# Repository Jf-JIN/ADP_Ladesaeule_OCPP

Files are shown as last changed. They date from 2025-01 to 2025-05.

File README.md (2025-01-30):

# ADP_Ladesaeule_OCPP

###### Aufgabeliste

谷歌表格: https://docs.google.com/spreadsheets/d/17lJi9eMh2AS8moNZEip401Un4izFQ7JtTx4U8HynT7c/edit?usp=sharing

###### Liste der zu bestellenden Komponenten

谷歌表格：https://excel.cloud.microsoft/open/onedrive/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

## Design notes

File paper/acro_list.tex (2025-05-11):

\begin{acronym}[MPC] % Give the longest label here so that the list is nicely aligned
%\acro{}{}  %sort alphabaticly
\acro{CS}{Charging Station}
\acro{CSMS}{Charging Station Management System}
\acro{CP}{Charging Pilot}
\acro{PP}{Proximity pilot}
\acro{EV}{Electric Vehicle}
\acro{GUI}{Graphical User Interfaces}
\acro{OCPP}{Open Charge Point Protocol}
\acro{V2G}{Vehicle-to-Grid}
\acro{TX}{Transmission}
\acro{RX}{Receiver}
\end{acronym}

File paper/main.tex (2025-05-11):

\documentclass[
	english,
	ruledheaders=section,%Ebene bis zu der die Überschriften mit Linien abgetrennt werden, vgl. DEMO-TUDaPub
	class=report,% Basisdokumentenklasse. Wählt die Korrespondierende KOMA-Script Klasse
	thesis={type=Report},% Dokumententyp Thesis, für Dissertationen siehe die Demo-Datei DEMO-TUDaPhd
	accentcolor=9c,% Auswahl der Akzentfarbe
	custommargins=true,% Ränder werden mithilfe von typearea automatisch berechnet
	marginpar=false,% Kopfzeile und Fußzeile erstrecken sich nicht über die Randnotizspalte
	%BCOR=5mm,%Bindekorrektur, falls notwendig
	parskip=half-,%Absatzkennzeichnung durch Abstand vgl. KOMA-Script
	fontsize=11pt,%Basisschriftgröße laut Corporate Design ist mit 9pt häufig zu klein
	logofile={img/tuda_logo.pdf}, %Falls die Logo Dateien nicht vorliegen
]{tudapub}

% Der folgende Block ist nur bei pdfTeX auf Versionen vor April 2018 notwendig
\usepackage{iftex}
\ifPDFTeX
	\usepackage[utf8]{inputenc}%kompatibilität mit TeX Versionen vor April 2018
\fi

%%%%%%%%%%%%%%%%%%%
%Sprachanpassung & Verbesserte Trennregeln
%%%%%%%%%%%%%%%%%%%
\usepackage[ngerman, main=english]{babel}
% \usepackage[english, main=ngerman]{babel}
% % 中文支持
% \usepackage{fontspec}
% \usepackage{xeCJK}  % LuaLaTeX 也适用

% % 设置中文字体
% \setCJKmainfont{Noto Serif CJK SC}  % 适用于简体中文
% \setCJKsansfont{Noto Sans CJK SC}   % 无衬线字体
% \setCJKmonofont{Noto Sans Mono CJK SC} % 等宽字体

% \usepackage[autostyle]{csquotes}% Anführungszeichen vereinfacht

% Falls mit pdflatex kompiliert wird, wird microtype automatisch geladen, in diesem Fall muss diese Zeile entfernt werden, und falls weiter Optionen hinzugefügt werden sollen, muss dies über
% \PassOptionsToPackage{Optionen}{microtype}
% vor \documentclass hinzugefügt werden.
\usepackage{microtype}
\usepackage{subcaption}
%%%%%%%%%%%%%%%%%%%
%Literaturverzeichnis
%%%%%%%%%%%%%%%%%%%
\usepackage{biblatex}   % Literaturverzeichnis
\bibliography{bibliography}
\usepackage{breakurl}
\usepackage{xurl} 

%%%%%%%%%%%%%%%%%%%
%Paketvorschläge Tabellen
%%%%%%%%%%%%%%%%%%%
%\usepackage{array}     % Basispaket für Tabellenkonfiguration, wird von den folgenden automatisch geladen
\usepackage{tabularx}   % Tabellen, die sich automatisch der Breite anpassen
%\usepackage{longtable} % Mehrseitige Tabellen
%\usepackage{xltabular} % Mehrseitige Tabellen mit anpassbarer Breite
\usepackage{booktabs}   % Verbesserte Möglichkeiten für Tabellenlayout über horizontale Linien
\usepackage{graphicx}
\usepackage{pdfpages}
\usepackage{enumitem}
\usepackage{xcolor}

\usepackage{float} 
\usepackage[acronym]{glossaries}
\usepackage{caption}
\captionsetup{justification=centering}
% acronyms
\usepackage{acronym}

%其他引用库
\usepackage{hyperref}
\usepackage{url}

%%%%%%%%%%%%%%%%%%%
%Paketvorschläge Mathematik
%%%%%%%%%%%%%%%%%%%
%\usepackage{mathtools} % erweiterte Fassung von amsmath
%\usepackage{amssymb}   % erweiterter Zeichensatz
%\usepackage{siunitx}   % Einheiten

%Formatierungen für Beispiele in diesem Dokument. Im Allgemeinen nicht notwendig!
\let\file\texttt
\let\code\texttt
\let\tbs\textbackslash
\let\pck\textsf
\let\cls\textsf

\usepackage{pifont}% Zapf-Dingbats Symbole
\newcommand*{\FeatureTrue}{\ding{52}}
\newcommand*{\FeatureFalse}{\ding{56}}

\begin{document}

\Metadata{
	title=ADP - Charging Station Upgrade to OCPP Communication for Smart Charging,
	author=Junfan Jin, Can Zeng, Yunan Jiang and Huang Chen
}

\title{ADP - Charging Station Upgrade to OCPP Communication for Smart Charging}
\subtitle{}
\author[J. Jin \and C. Zeng \and Y. Jiang \and H. Chen]{Junfan Jin \and Can Zeng \and Yunan Jiang \and Huang Chen}%optionales Argument ist die Signatur,
\birthplace{}%Geburtsort, bei Dissertationen zwingend notwendig
\reviewer{Prof. Dr. Stephan Rinderknecht \and M.Sc Thomas Franzelin \and Dr.Ing. Benjamin Blat-Belmonte}%Gutachter

%Diese Felder werden untereinander auf der Titelseite platziert.
%\department ist eine notwendige Angabe, siehe auch dem Abschnitt `Abweichung von den Vorgaben für die Titelseite'
\department{mb} % Das Kürzel wird automatisch ersetzt und als Studienfach gewählt, siehe Liste der Kürzel im Dokument.
\institute{IMS}
\group{}

\submissiondate{\today}
\examdate{\today}

% Hinweis zur Lizenz:
% TUDa-CI verwendet momentan die Lizenz CC BY-NC-ND 2.0 DE als Voreinstellung.
% Die TU Darmstadt hat jedoch die Empfehlung von dieser auf die liberalere
% CC BY 4.0 geändert. Diese erlaubt eine Verwendung bearbeiteter Versionen und
% die kommerzielle Nutzung.
% TUDa-CI wird im nächsten größeren Release ebenfalls diese Anpassung vornehmen.
% Aus diesem Grund wird empfohlen die Lizenz manuell auszuwählen.
%\tuprints{urn=XXXXX,printid=XXXX,year=2022,license=cc-by-4.0}
% To see further information on the license option in English, remove the license= key and pay attention to the warning & help message.

% \dedication{Für alle, die \TeX{} nutzen.}

\maketitle
\includepdf[pages=-]{Aufgabenstellung_ADP.pdf}

% \affidavit % oder \affidavit[digital] falls eine rein digitale Abgabe vorgesehen ist.

% Es gibt mit Version 3.20 die Möglichkeit ein Bild als Signatur einzubinden.
% TUDa-CI kann nicht garantieren, dass dies zulässig ist oder eine eigenhändige Unterschrift ersetzt.
% Dies ist durch Studierende vor der Verwendung abzuklären.
% Die Verwendung funktioniert so:
%\affidavit[signature-image={\includegraphics[width=\width,height=1cm]{example-image}}, <hier können andere Optionen wie z.B. affidavit=digital zusätzlich stehen>]

\tableofcontents

\clearpage
\textbf{Abbreviations} 
\input{acro_list}
\listoffigures
\listoftables

% chapter 1
\chapter{Introduction}
\label{chap: introduction}

% section 1.1
\section{Background}

% *************************** 文献 ***************************************
% Hassan, M., & Arefi, M. (2020). "Impact of electric vehicles on the power grid: A review of recent trends and future directions."
% Renewable and Sustainable Energy Reviews, 120, 109601.

% 这篇论文详细综述了电动汽车的普及对电网的影响，特别是高峰负荷期间电网压力增加的情况。

% Impact of electric vehicles on smart grid and future predictions: a survey
% https://www.researchgate.net/publication/366380176_Impact_of_electric_vehicles_on_smart_grid_and_future_predictions_a_survey
% https://www.energy.gov/sites/default/files/2024-10/Congressional%20Report%20EV%20Grid%20Impacts.pdf
% ************************************************************************

The development of internal combustion engine vehicles has spanned hundreds of years. However, with the advancement of \ac{EV} technology and growing environmental awareness, more and more \ac{EV}s are entering the consumer market. 

By 2024, the sales of \ac{EV}s had already reached six times those of 2018 \cite{EAutostatistik}, as shown in \autoref{fig: EVincreasing}. Similarly, the number of \ac{CS} increased by a factor of six, as illustrated in \autoref{fig: CSincreasing}. 

\begin{figure}[H]
    \centering
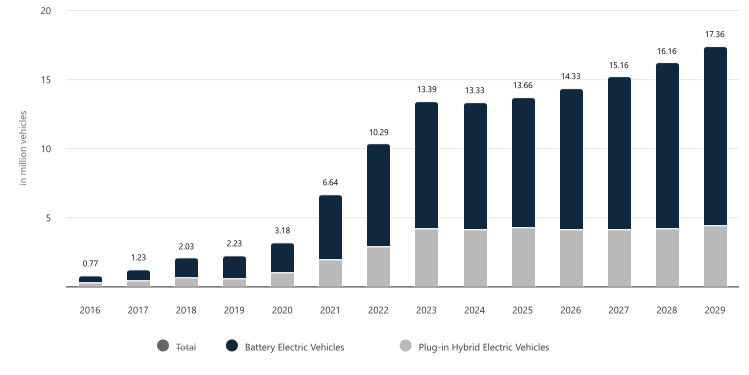
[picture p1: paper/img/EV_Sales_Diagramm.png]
     
    \caption{Electric vehicle sales increasing over the years
    (Source: \cite{EAutostatistik})}
    \label{fig: EVincreasing}
\end{figure}

\begin{figure}[H]
    \centering
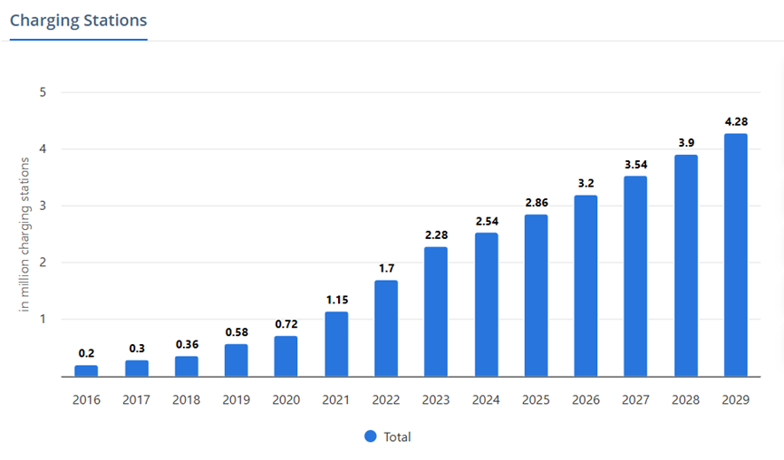
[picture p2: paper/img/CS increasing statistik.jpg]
     
    \caption{Charge station sales increasing over the years
    (Source: \cite{EAutostatistik})}
    \label{fig: CSincreasing}
\end{figure}

% 然而增加的电车数量也带来了挑战。传统的充电模式是即插即充，功率基本保持不变。在此充电模式下， 当电动汽车持有率较低时，电网对充电需求尚可以满足。然而随着持有率的增加，电网的负荷将逐渐加重，可能会导致电力系统诸多方面的问题，例如: Congestion, Simultaneity factor, Load characteristics, Generation assets connected at low voltage level, etc \cite{innovationOutlookSmartChargingForEV}. In Germany, “dumb” charging of electric vehicles under a 10 million electric vehicles by 2035 scenario would lead to a 50\% increase in low-voltage grid and transformer costs, while optimised peak shaving using smart charging would avoid these investments (Schucht, 2017)\cite{innovationOutlookSmartChargingForEV}.
Nevertheless, the rapid growth in the number of \ac{EV}s also poses significant challenges. Traditionally, charging adopts a "plug-and-charge" model, where the charging power remains constant. While the grid can accommodate charging demand at low \ac{EV} penetration levels, the rising number of \ac{EV}s is expected to impose a greater burden on the grid, particularly during peak demand periods.

In Germany, “dumb” charging of electric vehicles under a 10 million electric vehicles by 2035 scenario would lead to a 50\% increase in low-voltage grid and transformer costs. (Schucht, 2017)\cite{innovationOutlookSmartChargingForEV}.

% 为了应对上述挑战，智能充电（Smart Charging）技术应运而生。智能充电通过总和考量电价波动、用户偏好、用户需求、电网状态等诸多因素，对充电功率进行优化，为充电桩动态设计充电时间表，实现避免电网负载峰值和低谷的出现，降低充电成本，提升电网的稳定性。
To address these challenges, smart charging technology has emerged as a promising solution. Smart charging dynamically optimizes charging power by comprehensively considering multiple factors such as electricity price fluctuations, user preferences, charging demand, and grid conditions. By generating adaptive charging schedules for charging stations, smart charging helps to avoid grid load peaks and troughs, lower charging costs, and enhance grid stability.

% 综上所述，智能充电不仅是电动交通规模化发展的关键技术之一，也是支撑未来智慧电网（Smart Grid）和可再生能源大规模接入的重要手段。针对智能充电的建模、优化与控制策略研究，具有重要的理论价值和广阔的应用前景。
In summary, smart charging is not only one of the key technologies for the large-scale development of electric mobility but also a crucial enabler for the future smart grid and the large-scale integration of renewable energy sources. Research on the modeling, optimization, and control strategies of smart charging holds significant theoretical value and offers broad application prospects.

%With the development of electric vehicles, the demand for charging has also significantly increased, and charging stations can be seen everywhere. However, some charging stations still require users to configure settings to use it manually.  

%Therefore, this ADP aims to optimize and make the charging process intelligent. Users can get a better charging experience without too many input settings.

% section 1.2
\section{Research Significance}
%讲解ocpp的历史发展变迁

The necessity of smart charging lies in its ability to automatically generate a charging schedule based on known battery capacity and other relevant information. This enables the system to automatically adjust the charging rate according to different electricity pricing periods to realize peak shaving. This not only reduces charging costs but also reduces the peak load on the power grid.
Large-scale regulation of the power grid requires control over all charging stations within a given region, which means that these stations must adopt a unified charging protocol. Therefore, it is essential to develop \ac{CS} based on a standardized open-source protocol.

However, most charging stations do not use a unified communication protocol to standardize the charging process, which leads to compatibility issues when vehicles charge at different stations. Many manufacturers use their own closed-source charging protocols, such as the Nio Supercharger Protocol. The reliance on closed-source charging protocols significantly hampers compatibility and further limits the widespread adoption of smart charging.

The current mainstream open source charging protocol is \ac{OCPP} (refer to \autoref{sec: ocppLib}), which is therefore applied in this project.

% 在 OCPP 框架下，我们可以通过向充电桩发送控制消息，动态调整其输出功率，以适应不同的充电策略。根据实际需求，灵活调节充电时长和功率，为智能充电的实现提供了执行基础。
Under the \ac{OCPP} framework, it is possible to dynamically adjust the output power of charging stations by sending control messages, thereby accommodating various charging strategies. Based on actual requirements, the charging duration and power can be flexibly adjusted, providing an operational foundation for the implementation of smart charging.

%For other engineers who may wish to upgrade or modify the system based on this project, it is a huge advantage. However, the \ac{OCPP} library in Python does not implement certain functionalities.

%This project aims to optimize the code to address these shortcomings. Moreover, the \ac{OCPP} is continuously updated, e.g., from version 1.6 to 2.0.1. Each update can alter the library's content; for instance, the JSON files in \ac{OCPP} 2.0.1 contain much more nested information compared to those in \ac{OCPP} 1.6. Consequently, it is essential to optimize and upgrade charging stations based on the latest \ac{OCPP} version to ensure improved functionality and compatibility. 

% section 1.3
\section{Objectives}

%At the beginning of the project, the Institute for Mechatronic Systems (IMS) provided an existing \ac{CS} equipped with two buttons: one for starting the charge and the other for stopping. The device could only charge at a fixed rate, and the charging process had to be started and stopped manually. 
% 因此该项目的目标就是改进一个由IMS所提供的CS。这个CS只有2个按钮，只能实现基本功能。

% 该 ADP 的目标是修改机电系统研究所 (IMS) 提供的现有 CS，以实现智能充电。
The objective of this ADP is to modify an existing \ac{CS} provided by the Institute for Mechatronic Systems (IMS) to achieve intelligent charging.

This \ac{CS} is very primitive and can only be operated by two buttons: one for starting the charge and the other for stopping. The device could only charge at a fixed rate, and the charging process had to be started and stopped manually.

% The tasks are divided into two parts: software and hardware.

% On the software side, the focus is on enabling communication based on various protocols, such as \ac{OCPP}, WebSocket, and Modbus, ensuring that different systems can successfully exchange requests and responses to control the charging current.

% Hardware selection is based on the software functionalities.

% The hardware firstly supports the control of the logical current, as well as the connection and disconnection of charging current via a contactor. In addition, three-phase current and voltage will also be monitored.

% 该项目的主要内容为以下几点：
% 搜索并阅读现有的有关标准化充电基础设施和智能充电的文献
% 了解现有的充电站情况
% 对旧的充电站进行技术升级，让它支持OCPP通信协议
% 完成一个智能充电系统的样机的搭建
% 测试并调试智能充电站的功能

The main contents of this project are as follows:
\begin{itemize}
    \item Search and read existing literature on standardized charging infrastructure and smart charging
    \item Learn about the existing \ac{CS}
    \item Upgrade the old \ac{CS} to support the \ac{OCPP} communication protocol
    \item Complete the construction of a prototype of a smart charging system
    \item Test and debug the functions of the smart \ac{CS}
\end{itemize}

After the charging station is upgraded, in addition to manual control for starting and stopping charging, it should also be capable of charging according to a preset charging schedule, dynamically adjusting the charging power, and even automatically generating an optimal charging plan based on user preferences or electricity prices, and executing it autonomously.

%The ultimate goal is to achieve peak shaving, allowing charging stations to charge vehicles with low power during peak electricity demand periods, thereby reducing the burden on the power grid and preventing overload.

% section 1.4
\section{Overview}
%主要讲论文结构

% 第二章主要介绍项目涉及的硬件，包括低压和高压组件。逻辑控制部分属于低压部分，而高压部分主要由接触器和220V电源组成。

In Chapter 2, the hardware involved in the project and the overall connection structure of the \ac{CS} are mainly introduced.

% 第三章介绍了充电桩系统和优化器系统的基本架构，以及这两个系统与硬件之间的通信方式。本章介绍了OCPP Python库的使用方法及其局限性、系统如何获取OCPP消息以及如何通过生成器生成消息而无需每次都检查JSON文件、信号的实现以及异步隔离。

Chapter 3 introduces the basic architecture of the Charge Point System and the Optimizer System, as well as the communication methods between these two systems and the hardware. It covers how the \ac{OCPP} Python library is used together with its limitations, how the system obtains \ac{OCPP} messages and generates messages without every time to check JSON files through a generator, the implementation of signals, and asynchronous isolation.

% 第四章介绍了优化器的一些基本方法、优化过程中涉及的考虑因素、充电成本、时间、成本、约束条件和目标的定义，以及主要功能服务器。

Chapter 4 introduces some fundamental methods of the optimizer, the considerations involved in optimization, the definitions of charging cost, time, costs, constraints, and objectives, as well as the main function.

% 第五章主要介绍充电执行逻辑、模块设计和功能，包括充电单元模块、充电数据管理器模块、用于硬件轮询的线程管理模块、Modbus通信模块和GPIO管理器模块。

Chapter 5 mainly introduces the charging execution logic, module design, and functions, including the charging unit module, charging data manager module, thread management module for hardware polling, Modbus communication module, and GPIO manager module.

% 第六章主要介绍如何实现一个 \ac{GUI} 来显示和管理充电数据。

Chapter 6 mainly describes how to implement a \ac{GUI} to display and manage charging data.

% 第七章介绍了两种测试 \texttt{CS} 的方法：软件仿真和实验室测试。模拟器在实验室进行实际测试之前提供了一个虚拟平台。从功能上讲，模拟器分为两部分：一部分通过读写 JSON 文件来模拟系统与 EVSE 之间的通信；另一部分通过模拟 HTTP 服务器来模拟 Shelly 信号。测试部分涵盖了测试过程中出现的问题和结果。

Chapter 7 introduces two steps to test the \ac{CS}, namely simulation over software and testing in the lab, and the issues that occurred during testing and the results.

%. Simulator offers a fictitious platform before real-world testing in the lab. Functionally, the simulator is divided into two parts: one part simulates communication between the system and the EVSE by reading and writing JSON files; the other part simulates Shelly signals by emulating an HTTP server. The testing section covers the issues that occurred during testing and the results.

% 最后一章介绍了结果评估、目标实现情况以及系统可能的改进方向。

The last Chapter is about the evaluation of results, how many goals are achieved, and a discussion about the possible improvement of this system.

%注释掉的部分考虑可以放到hardware/software introduction
%The internal structure of the charging station is mainly divided into two parts. The first part is the high-voltage part, which includes components such as the power supply, contactor, RCD, and Shelly. This part is responsible for supplying current, monitoring power, and limiting the current to protect users. The second part is the low-voltage section, which handles the charging logic. It consists of a Raspberry Pi, relays, and a level shifter. Additionally, a DC motor controls the locking mechanism of the charging cable. All components are mounted on a DIN rail.

%For the logic control part, the Raspberry Pi offers two charging options. The first option allows users to start charging directly by pressing the start button on the charging station, supplying an AC current of 16A. Charging continues until the stop button is manually pressed. The second option involves using HTML to input vehicle information into the Raspberry Pi, including total charging amount, departure time, maximum/minimum current, maximum voltage, and charging mode. The Raspberry Pi then sends an \ac{OCPP}-format charging needs request message to the optimize system via WebSocket. After optimization, the optimize system returns a set charging profile request message containing the charging schedule. Once the Raspberry Pi receives the charging schedule and confirms that Shelly and EVSE are ready, it initiates the charging process. The optimize system mainly implements a peak-shaving function. During charging, Shelly monitors the charging current and voltage. The Raspberry Pi periodically sends updated charging demand data to the optimize system to refresh the charging schedule.

% % section 1.5
% \section{Structure}

% chapter 2
\chapter{Hardware Introduction}
%为什么
%Hardware is one of the foundations of this project. This includes identifying which electrical functions are required, which components are responsible for logical control, and explaining the function and working logic of each hardware component. 
%目的
%智能充电的实现首先需要硬件的支持，为了实现这个目的，我们的智能充电桩采用了如下硬件。
The implementation of smart charging first requires hardware support. To achieve this, our smart charging station is built using the following hardware components:
%Our goal is to use two parts, the first part is responsible for power supply and cut-off to the vehicles, the second part outputs the control logic signals according to the software system.
% 本项目主要使用到如下硬件：raspberry pi 3B；Shelly Pro 3EM； ESB 40-40； \texttt{EVSE\_WB}； 双通道继电器； level shifter; 充电桩本体。
%怎么完成
Raspberry Pi 3B (\autoref{sec: Raspberry Pi}), EVSE WB and Contactor AF30-30-00-13 (\autoref{sec: EVSE and Contactor}), Shelly Pro 3EM (\autoref{sec: Shelly Pro 3EM}), Power supplies of different voltages (\autoref{sec: power supply}), level shifter (\autoref{sec: level shifter}), dual channel relay and DC motor (\autoref{sec: relay and motor}), charge plug (\autoref{sec: connector}) and the original charging point.

%这些硬件实现了搭载程序，控制功率输出，给各部件提供电源，转换通讯电压，输出功率测量等功能。
These hardware components enable functions such as running embedded programs, controlling power output, supplying power to various modules, converting communication voltages, and measuring output power.
% 我们将这些部件组装在了充电桩内部的轨道上，简单连接如图。
We assembled these components on the track inside the charging station, and the simple connection is shown in \autoref{fig: simple circuit}.

\begin{figure}[H]
    \centering
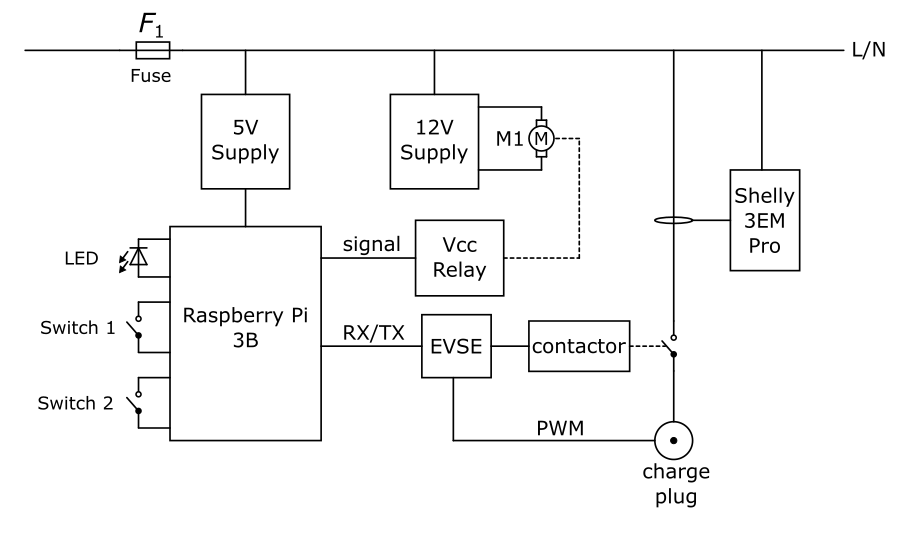
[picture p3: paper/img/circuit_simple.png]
     
    \caption{simple circuit}
    \label{fig: simple circuit}
\end{figure}

\section{Raspberry Pi}
\label{sec: Raspberry Pi}
% 树莓派是该项目程序的载体，用于连接和控制其他硬件（如shelly和EVSE），并处理和上报硬件获取的信息（如已经完成的充电量，当前输出电流等），处理并上报错误信息等。树莓派通过websocket和软件通讯，并按照优化系统计算的充电计划，将计算后的充电电流值发送到EVSE。
% 该项目使用的树莓派型号为raspberry pi 3B。

Raspberry Pi is the carrier of the main charging program, which is used to connect, control, and communicate with other hardware (such as Shelly and EVSE), process or send the data obtained by the hardware (such as the total charged energy, current output, etc.), and process and report errors, etc. Raspberry Pi communicates with the \ac{CSMS} through WebSocket and sends the target charging current value to EVSE according to the charging plan calculated by the optimization system.
The Raspberry Pi model used in this project is Raspberry Pi 3B. The pin-out of Raspberry Pi 3B is shown in \autoref{fig: Raspberry Pi overview}.

\begin{figure}[H]
    \centering
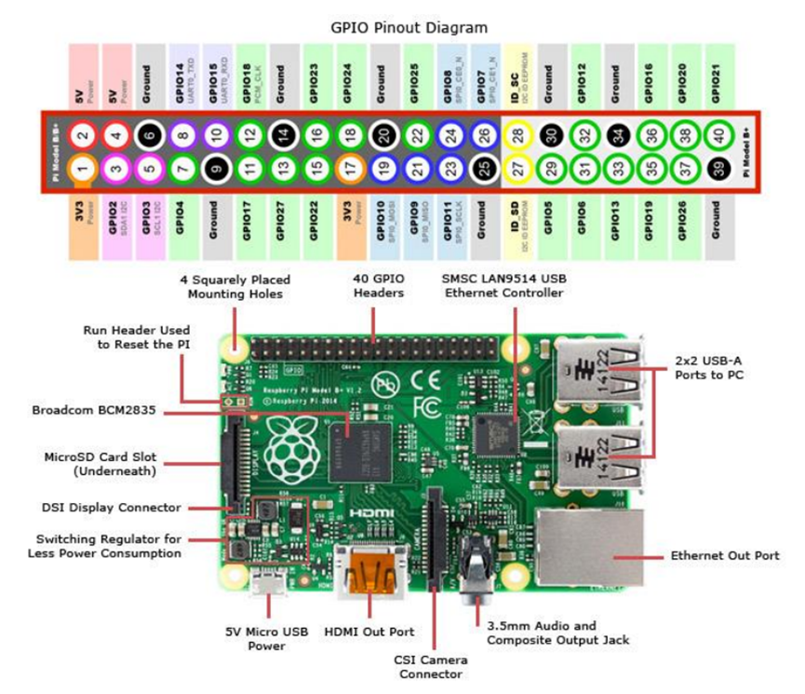
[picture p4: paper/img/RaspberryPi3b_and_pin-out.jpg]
     
    \caption{Raspberry Pi 3B and its pin-out overview
    (Source: \cite{RaspberryPiOverview})}
    \label{fig: Raspberry Pi overview}
\end{figure}

\paragraph{Remote control of Raspberry Pi}
% 在树莓派装载操作系统后，可以连接外置显示器和键盘对树莓派的Ubuntu系统进行环境配置，安装软件等操作。为了便于调试和操作，我们使用JupyterLab对Ubuntu系统进行访问，并以此作为启动python脚本的方式。为了实现远程控制，我们通过固定wifi账户和密码的方式，让树莓派启动后自动连接到预先设置的wifi，之后使用连入同一wifi的其他设备（如笔记本电脑）使用Jupyterlab接入树莓派的IP地址，这样就能在只给树莓派提供电源的情况下远程进入树莓派的控制界面。使用Wifi连接也有利于树莓派和Shelly传感器通过HTTP请求进行沟通。

After the Raspberry Pi is loaded with the operating system, it is possible to configure the environment of the Raspberry Pi's Ubuntu system, install software, or perform other operations with an external monitor and keyboard. For easier debugging and commissioning, we use JupyterLab to access the Ubuntu system and use it to launch the Python script. In order to achieve remote control, we first connect the Raspberry Pi with a fixed WiFi account and password. In this way, the Raspberry Pi can automatically connect to this pre-set WiFi after startup. And then another device (such as a laptop) can be connected to the same WiFi to remotely access the control interface of the Raspberry Pi by providing Jupyterlab the IP address of the Raspberry Pi to get access. By doing so, the Raspberry Pi becomes remotely controllable with only a power supply as a necessity. Using WiFi connection also facilitates communication between the Raspberry Pi and the Shelly sensor via HTTP requests.
% \paragraph{connection between Raspberry Pi and EVSE }
% 树莓派与EVSE通过Modbus连接(Refer to section\autoref{sec:modbusIntroduction})。为此需要用到树莓派的UART接口。在raspberry 3B上提供了Primary UART，使用GPIO 14 (transmit) and 15 (receive)作为输入输出pin。由于3B的Primary UART是mini UART，需要在使用前进行配置，在树莓派的config.txt 文件中设置\texttt{enable\_uart=1},以设置固定的时钟频率。此时这个UART接口在树莓派中的地址为/dev/serial0。通过pymodbus库，我们利用这个接口和EVSE建立modbus通讯。\cite{miniUART}
% 由于树莓派使用3.3V系统，而EVSE使用5V系统，这个modbus通讯的线路需要连接一个level shifter 用以转换电压，避免树莓派被损坏。连接方式见线路图。

The Raspberry Pi is connected to the EVSE via Modbus (Refer to \autoref{sec: modbus}). By default, the primary UART of the Raspberry Pi 3B is assigned to the Linux console. To use the primary UART for other purposes, it is necessary to reconfigure Raspberry Pi OS by using raspi-config. After this configuration, we can use the serial port \texttt{/dev/ttyS0} and with the support of the pymodbus library to establish Modbus communication with the EVSE. \cite{serialport}
Due to the fact that the Raspberry Pi uses a 3.3V system and the EVSE uses a 5V system, these Modbus communication lines need to be connected with a level shifter to convert the voltage to avoid damage to the Raspberry Pi. Refer to the circuit diagram for the connection method (\hyperref[add:Ladestation_v2R]{Ladestation\_v2R}).

\paragraph{Connection between Raspberry Pi and Shelly pro 3EM}
The Raspberry Pi and Shelly sensor are not physically connected in this project. Instead, the communication is achieved via HTTP requests. Since the charging station uses a three-phase AC power supply, we apply the Shelly Pro 3EM sensor, which provides three current clamps to measure real-time current and total charged energy for each phase. The Raspberry Pi obtains this data and monitors sensor status by sending periodic HTTP requests. This information is used to adjust the charging plan, detect errors, or display.

\section{EVSE and Contactor}
\label{sec: EVSE and Contactor}

EVSE stands for electric vehicle supply equipment. It is an element that supplies electric energy for the recharging of electric or plug-in vehicles. 

In order to adjust the current output, the hardware EVSE must be used to adapt the high-power input from the supply network to the user's side. In this case, EVSE WB is used which connects to the level shifter from 3.3V to 5V, obtaining the communication signals with \ac{RX} and \ac{TX}. \ac{RX} and \ac{TX} are directly controlled by Raspberry Pi. 
%The EVSE WB consumes power fewer than 1 W while letting the default current setting 13A which meets our needs \cite{EVSEdatasheet}.

% EVSE通过充电枪上的CP接口，以PWM信号的形式将允许的充电电流大小值传输到充电车辆，并根据电压的level判断车辆状态。EVSE WB有3个连接头，X1用于和高压端的电网相连，给EVSE各组件供电（例如产生PWM信号的继电器），X2包含连接充电枪的CP接口，判断允许电流的PP接口，以及其他功能。还有一个用于控制的PROG接口。本项目利用PROG接口进行Modbus通讯。通过Modbus通讯，树莓派对EVSE各寄存器进行读取和写入操作，直接控制输出电流的大小，并获取车辆及EVSE状态。由于我们不会更改充电枪的电缆，所以我们通过在X2接口的PP接口和GND接口间接入固定电阻的方式，将最大许用电流限制在32A。

EVSE transmits the allowed charging current value to the charging vehicle in the form of a PWM signal through the \ac{CP} terminal on the charging plug, and determines the vehicle status based on the feedback voltage level in this terminal. EVSE WB has 3 connectors. Connector X1 is connected to the high-voltage power grid to power the EVSE components (such as the relay that generates the PWM signal). Connector X2 includes the \ac{CP} terminal, which leads to the same terminal on the charging plug, the \ac{PP} terminal for determining the allowed current, and other auxiliary terminals. There is also a PROG connector for control. In this project, we use the PROG connector for Modbus communication. Through Modbus communication, the Raspberry Pi can read and write the EVSE registers. This enables the Raspberry Pi to directly control the output current and obtain the vehicle and EVSE status. Since we will not change the cable of the charging plug, the maximum allowable current is limited to 13A (Although the cables can handle a current of 32A, the maximum current is limited to 13A to meet laboratory requirements.) by installing a fixed resistor between the \ac{PP} terminal and the GND terminal of connector X2 \cite{EVSEdatasheet}.

% AF30-30-00-13是一个接触器，受EVSE控制（通过X1的rel通道）。它的额定工作电流达到50A AC,适配本项目的工作情况。\cite{AF30-30-00-13}Unlike lower-powered relays, contactors generally have special structures for arc-suppression to allow them to interrupt heavy current。通过这个接触器，EVSE只会在状态正常时接通电路，。

AF30-30-00-13 (as shown in \autoref{fig: AF30-30-00-13}) is connected to the rel pin on EVSE 4-pin side and controlled by the EVSE via the relay channel of X1. Its rated operating current is 50A AC\cite{AF30-30-00-13}, suitable for the requirements of this project. Unlike lower-powered relays, contactors typically have specialized structures for arc suppression, enabling them to interrupt heavy currents. With this contactor, the EVSE will only connect the circuit when the system is in a normal state.

\begin{figure}[htbp]
    \centering
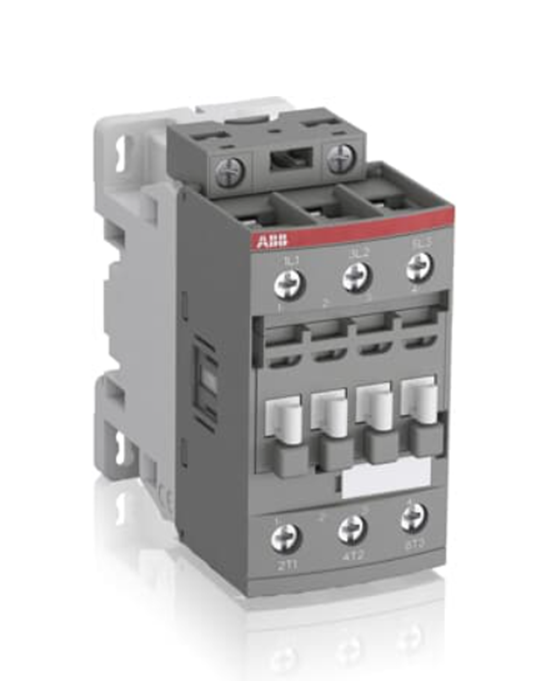
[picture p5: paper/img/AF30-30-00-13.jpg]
    
    \caption{AF30-30-00-13
    (Source: \cite{AF30-30-00-13})}
    \label{fig: AF30-30-00-13}
\end{figure}

\section{Shelly Pro 3EM}
\label{sec: Shelly Pro 3EM}
% 由于我们使用三相交流电，所以我们选择了这款传感器。它的特点是具有3个电流钳，分别测量3个相的电流，电压，还可以记录已经完成的充电量。通过HTTP请求，我们可以获取测量数据，并对传感器进行控制。从Shelly传感器获取的数据为充电计划表的校正更新提供了支持，是智能充电桩动态调整充电计划的基础。在一次充电完成后，我们需要通过\texttt{reset\_totals}命令分别清除每个电流钳的累计消耗能量，将总充电量清零，以便下一次充电。

Since the charging point uses three-phase AC, we chose Shelly Pro 3EM. As shown in \autoref{fig: Shelly Pro 3EM}, Shelly Pro 3 EM can be assembled on DIN rail. It features three current clamps that measure the current and voltage of the three phases respectively, besides it also records the charged energy. Through HTTP requests, we can obtain measurement data as well as control the sensor. The data obtained from the Shelly sensor provides support for the correction and update of the charging schedule and is the basis of the dynamic charging plan adjustment of the smart charging point. After a charge is completed, we need to clear the accumulated energy consumption of each current clamp separately through the \texttt{reset\_totals} command and reset the total charged energy value to zero for the next charge.

\begin{figure}[htbp]
    \centering
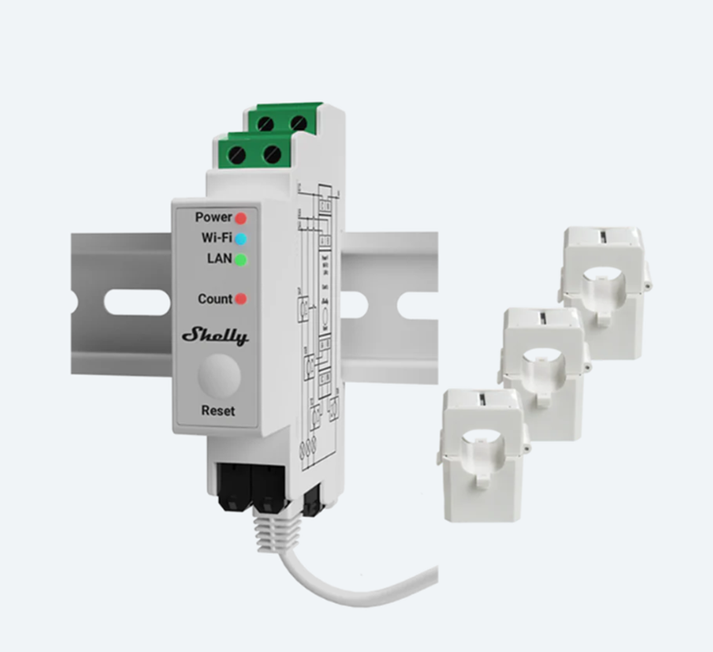
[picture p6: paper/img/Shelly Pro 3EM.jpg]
    
    \caption{Shelly Pro 3EM
    (Source: \cite{Shelly})}
    \label{fig: Shelly Pro 3EM}
\end{figure}

% \section{Original CS}
% \label{sec: Original CS}
% % 本项目改造的充电桩，只具有基本的充电功能，无法控制充电功率。内部有
% % Residual Current Circuit Breaker （F204 B-40），Circuit Breaker（S451E）等组件。

% The charging point to be modified in this project only has basic charging functions and cannot control the charging power. It contains components such as Residual Current Circuit Breaker (F204 B-40) and Circuit Breaker (S451E).

\section{Power Supply (3.3V 5V 12V)}
\label{sec: power supply}

In this system, different hardware requires four kinds of voltage supply. The 220V network serves as the power source from which voltage levels such as 3.3V, 5V, and 12V are derived. 

Firstly,  STEP3-PS from Phoenix Contact provides 5V voltage for Raspberry Pi on the input side. Then, Raspberry Pi outputs 5V voltage as Vcc for the relay and the high-voltage side on the level shifter. Secondly, the Uno-power, a 12V DC power supply from Phoenix Contact, transforms 220V into 12V voltage which supplies the relay. Meanwhile, Raspberry Pi outputs signals with 3.3V on GPIO14 and GPIO15, which will be converted by the level shifter into 5V signals to EVSE. The electrical connection is demonstrated by the circuit diagram in the appendix.

% \section{Other component}
% \label{sec: Other component}
% \paragraph{Power supply}
% % 我们增加了5V和12V的两个电源，5V电源给树莓派供电，12V电源给双通道继电器和电机供电。

% Two power supplies of 5V and 12V are added to the charging point. The 5V power supply is used to power the Raspberry Pi, and the 12V power supply is used to power the dual-channel relay and DC motor.

\section{Level shifter}
\label{sec: level shifter}
% EVSE和树莓派之间通过Modbus通讯，但由于两个系统的工作电压不同，需要在Modbus通讯线路之间通过level shifter转换电压，避免损坏树莓派。同时为了方便固定安装，我们建模打印了一个安装底座将树莓派，level shifter和relaies安装在了一起，如图所示。

The EVSE and Raspberry Pi communicate via Modbus, but because of the different operating voltages of the two systems, a level shifter is installed to convert the voltage between the Modbus communication lines to avoid damaging the Raspberry Pi. In order to facilitate fixed installation, we modeled and printed a mounting base to install the Raspberry Pi, the level shifter, and the relay together, as shown in \autoref{fig: RaspberryPi board}.

\begin{figure}[H]
        \centering
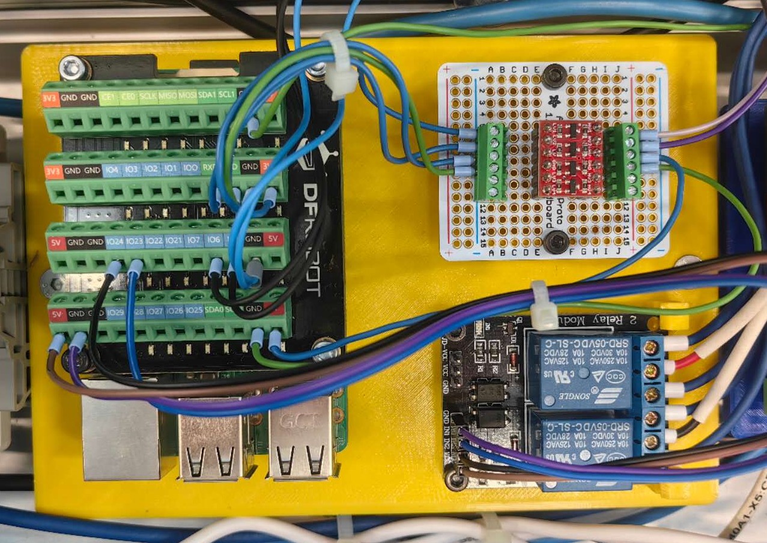
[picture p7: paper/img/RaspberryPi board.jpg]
        
        \caption{RaspberryPi board}
        \label{fig: RaspberryPi board}
    \end{figure}

\section{Dual channel relay and DC motor}
\label{sec: relay and motor}
% 直流电机用于锁止充电枪，避免在充电过程中，充电枪被意外拔出。电机和一个闸相连，电机正转时合闸，锁住充电枪，电机反转时释放闸。电机的正反转是通过改变直流电机两端电压方向实现的。为此我们使用一个双通道继电器来实现此功能。1号通道的NO端和2号通道的NC端接GND，一号通道的NC端和2好通道的NO端接12V电压，直流电机的两端接两个通道的COM口，这样就可以通过控制继电器开闭来改变电机转动方向。在脚本中设置了电机正反转的时间，避免锁止后电机继续长时间工作而损坏。继电器通过树莓派的两个GPIO接口控制(GPIO23/GPIO24),
% 仅需通过拉高接口的电平即可控制开闭（我们使用gpiozero库的LED命令完成这个操作）。

The DC motor is used to lock the charging plug to prevent the charging plug from being accidentally pulled out during the charging process. The DC motor is connected to a latch. When the motor rotates forward, the latch is closed to lock the charging plug, and when the motor rotates reversely, the latch is released. The forward and reverse rotation of the motor is achieved by changing the direction of the voltage at both ends of the DC motor. For this purpose, we use a dual-channel relay to realize this function. The NO end of channel 1 and the NC end of channel 2 are connected to GND, the NC end of channel 1 and the NO end of channel 2 are connected to 12V voltage output, and the two ends of the DC motor are connected to the COM ports of the two channels, so that the direction of rotation of the motor can be changed by controlling the opening and closing of the relay. The forward and reverse rotation time of the motor is limited in the script to prevent the motor from being damaged by continuing to work for a long time after locking (or releasing). The relay is controlled by two GPIO terminals of the Raspberry Pi (GPIO23/GPIO24). The opening and closing can be controlled by simply pulling up the voltage level of the terminals (we use the LED command of the gpiozero library to complete this operation).

% section 2.5
\section{Connector}
\label{sec: connector}
%这里带过介绍下其他的connectors 然后要先介绍Typ 2 Connector

In this project, an IEC 62196-2 Typ 2 connector is used, which has seven pins. L1, L2, and L3 correspond to the three-phase power lines, while N represents the neutral line. \ac{PP} and \ac{CP} are signal lines for pre- and post-insertion signalling, respectively. PE is the ground wire. 

\begin{figure}[H]
    \centering
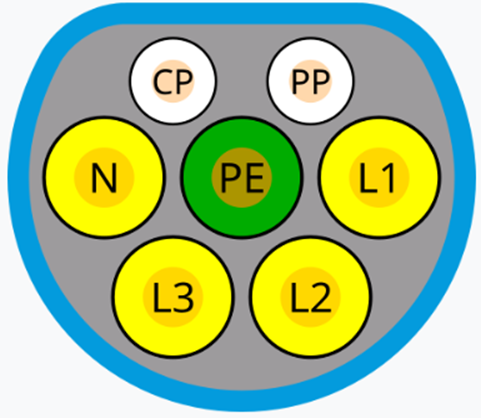
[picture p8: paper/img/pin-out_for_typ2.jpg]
     % 这里替换成你的图片文件名
    \caption{pin-out for typ2 connector
    (Source: \cite{IECStandard})}
    \label{fig:typ2pin-out}
\end{figure}

There are other connector standards, such as SAE J1772 also known as IEC 62196-2 Typ 1, which is implemented in North America but only supports single-phase AC. Another example is Tesla's SAE J3400, which supports both single-phase AC and DC charging.

% section 2.1
% \section{EVSE and AC Contactor}

% In order to adjust the current output, the hardware EVSE must be used to adapt the high power input from the supply network to users side. In this case, EVSE WB is used which connects to the level shifter from 3.3 V to 5 V obtaining the communication signals with RX and TX. RX and TX are directly controlled by Raspberry Pi. The EVSE WB consumes power fewer than 1 W while letting default current setting 32 A through which meets our needs\cite{EVSEdatasheet}.

% Meanwhile, EVSE WB is equipped with PP function. It detects the abnormal current passing through cable\cite{typ2connector}.  However, for an additional protection from Leakage current, AF30-30-00-13 is connected to rel on EVSE 4-pin side. The maximal working current of AF30-30-00-13 reaches 40 A\cite{AF30-30-00-13}.

% \begin{figure}[htbp]
%     \centering
%     \includegraphics[width=0.3\textwidth]{img/AF30-30-00-13.jpg}
%     \caption{AF30-30-00-13
%     (Source: \cite{AF30-30-00-13})}
%     \label{fig:AF30-30-00-13}
% \end{figure}

%插入下 EVSE 的图 （最好自己拍一个？）

% section 2.2
% \section{Shelly}

% On the load side, it's necessary to monitor the output. Shelly Pro 3 EM captures current, voltage and power by means of flux variation and can be connected with WiFi to transmit the data. As shown in the figure (\autoref{fig:Shelly Pro 3EM}), Shelly Pro 3 EM can be assembled on DIN rail.

% \begin{figure}[htbp]
%     \centering
%     \includegraphics[width=0.4\textwidth]{img/Shelly Pro 3EM.jpg} % 这里替换成你的图片文件名
%     \caption{Shelly Pro 3EM
%     (Source: \cite{Shelly})}
%     \label{fig:Shelly Pro 3EM}
% \end{figure}

% section 2.3
% \section{Raspberry Pi 3 Model B+}
% \label{sec:RaspberryIntroduction}

% Raspberry Pi 3B is one of the most important hardware in this case. It has mainly 2 tasks. The first task is to communicate with EVSE through RX and TX to control output voltage. Besides that, Raspberry Pi gives signal to relays in order to drive the locking motor. The overview, the pin-out of Raspberry Pi 3b and communicates via OCPP (\autoref{fig:Raspberry Pi overview}) are shown below.

% \begin{figure}[H]
%     \centering
%     \includegraphics[width=0.7\textwidth]{img/RaspberryPi3b_and_pin-out.jpg} 
%     \caption{Raspberry Pi 3b and its pin-out overview
%     (Source: \cite{RaspberryPiOverview})}
%     \label{fig:Raspberry Pi overview}
% \end{figure}

%得补充引脚？
%图片插入的位置不对，后期再调整

% section 2.4
% \section{Power Supply (3.3V 5V 12V)}

% In this system, different hardware require totally four kinds of voltage supply. The 220V network serve as the power source from which voltage levels such as 3.3V, 5V and 12V are adapted. 

% Firstly, Phoenix STEP3-PS provides 5V 3A current for Raspberry Pi on the input side. Then, Raspberry Pi outputs also 5V voltage not only as Vcc for relay but also for level shifter on the high voltage side. Secondly, Mean Well NDR75-12 transforms 220V into 12V 6.3A current which supplys the relay. Meanwhile, Raspberry Pi outputs signals with 3.3V on GPIO14 and GPIO15, this will be converted by level shifter into 5V signals to EVSE. The electrical connection is demonstrated by circuit diagram in appendix.

% section 2.5
% \section{Connector (Typ 2)}

% In this project, a IEC 62196-2 connector (Type 2) is used, which has seven pins. L1, L2, and L3 correspond to the three-phase power lines, while N represents the neutral line. PP and CP are signal lines for pre- and post-insertion signalling, respectively. PE is the ground wire. 

% \begin{figure}[H]
%     \centering
%     \includegraphics[width=0.3\textwidth]{img/pin-out_for_typ2.jpg} % 这里替换成你的图片文件名
%     \caption{pin-out for typ2 connector
%     (Source: \cite{typ2connector})}
%     \label{fig:typ2pin-out}
% \end{figure}

% % section 2.6
% \section{Motor and relay}

% Connection between CS and charging cable can be flexibly established or removed. To prevent accidental unplugging of the charging cable during charging, which could lead to electric shock incidents, a motor is installed at the interface of the charging station to lock the cable in place during charging, making it impossible to unplug the cable. The motor's forward and reverse rotation is controlled by a dual-channel relay. 

% % 继电器的电路导通细节应该简单的介绍吗？

% chapter 3
\chapter{System Base}

\label{chap:SystemBase}

% This chapter mainly introduces the design of the software's framework for the project which is used between the optimizer and the Raspberry Pi charging station. It includes the following aspects:

% \begin{enumerate}
%     \item The Frame of Systems
%     \item The design of WebSocket communication ports.
%     \item Methods for obtaining and generating OCPP data
%     \item The adaptation of the official library
%     \item The design of the signal-slot construct
%     \item Application and isolation of synchronous and asynchronous programming
% \end{enumerate}

%软件底层作为本项目的基石，是十分重要且必要的一部分，优秀的底层设计能使系统整体更加稳定，运行速度更加快速，拓展性更高。在本章中主要是介绍了该项目系统框架的软件底层部分中用到的设计，其在优化器与树莓派充电桩部分中共同使用，包括系统框架简介，\texttt{WebSocket}通讯端口设计，获取OCPP数据的方式，生成OCPP数据的方式，对于官方库机制的使用以适配，信号槽机制的设计，同步与异步编程的使用与隔离

%为什么

This chapter illustrates the division of the system structure using class diagram and how to use 4 modules from the official \ac{OCPP} library. It gives an instruction to the workflow.

%目标+怎么做
The workflow contains steps from obtaining \ac{OCPP} data to generating \ac{OCPP} data using message generator and how to adapt the signal-slot mechanism. Besides that, the synchronous and the asynchronous modules are isolated using message queue.

\section{System Frame}
\label{sec:SystemFrame}

\begin{figure}
    \centering
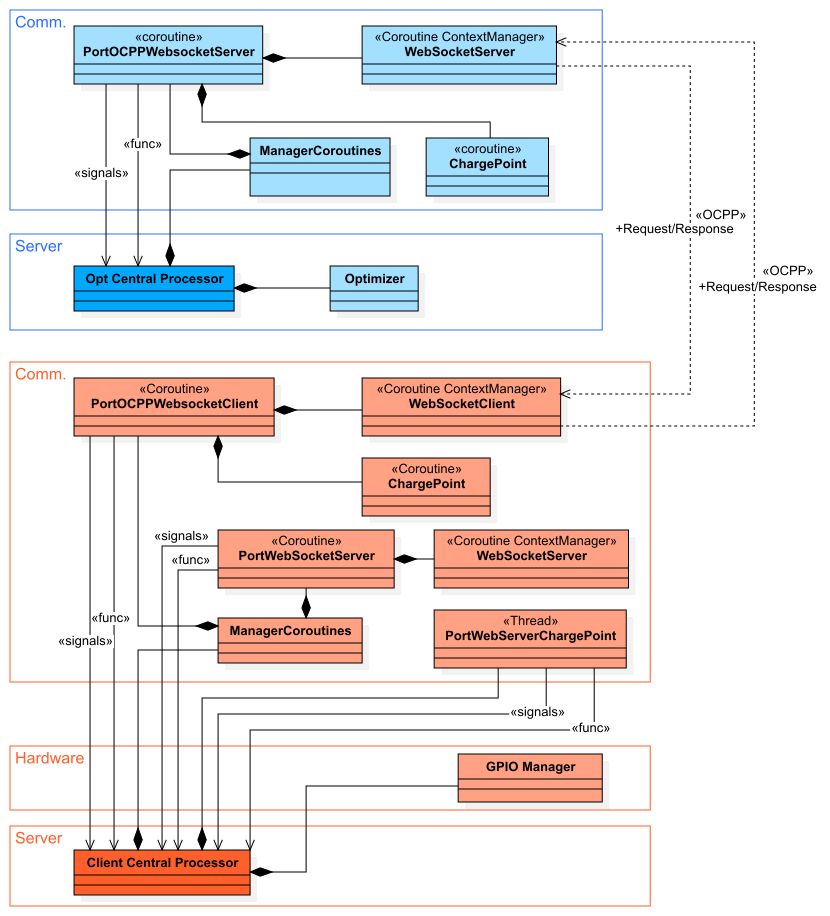
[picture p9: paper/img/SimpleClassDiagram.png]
     
    \caption{System Frame}
    \label{fig: SystemFrame}
\end{figure}
% 本项目主要包含两个核心系统：充电桩系统和优化器系统，二者的功能和结构相似，如上图所示。优化器系统由两个主要模块构成：通讯层和服务层。通讯层负责接收各类消息并进行解析，能够处理OCPP（开放充电桩协议）消息、图片、文本消息等格式，此外还需要管理和维护与网页服务器的通信，确保数据流畅传递至客户端界面。服务层则是优化器系统的核心，主要负责处理具体的优化器业务逻辑，包括计算充电计划表、负载均衡以及数据分析等功能。

% 充电桩系统除了包含优化器系统的通讯层和服务层外，还增加了一个硬件层，这一层的主要职责是管理硬件设备（如充电桩硬件、传感器等）并与硬件进行通讯。硬件层与系统其他部分的集成非常重要，它确保硬件设备能够正常工作并实时反馈状态。硬件层的数据处理还涉及到对充电桩的开关控制、计划表执行、故障检测等多项功能。

% 在充电桩系统的通讯层，除了基本的消息接收和解析功能外，还特意增加了WebSocket端口功能。这个WebSocket端口是为了支持与未来可能开发的新设备进行通讯。这一设计为系统的扩展性提供了便利，使得在今后新设备或功能的加入时，不会受到当前通讯方式的限制。

% 此外，两个系统间通过WebSocket端口进行通信

% *********************************************
% 需求 -> 目的 -> 实现

This project features a relatively complex system architecture with numerous functionalities to implement, such as \ac{OCPP} message processing and generation, charging logic control, and charging process optimization. Therefore, an effective solution is to decompose the entire large system into multiple subsystems, with each subsystem responsible for a major function\cite{Softwarearchitecture}. This approach will significantly facilitate testing and debugging.

This project primarily consists of two core systems: the charging point system and the optimizer system. The functionalities and structures of these two systems are similar, as illustrated in \autoref{fig: SystemFrame}.

The Optimizer System is composed of two main modules: the Communication Layer and the Service Layer. The Communication Layer is responsible for receiving and parsing various types of messages, including \ac{OCPP} messages, images, and text messages. Additionally, it manages and maintains communication with the webserver to ensure smooth data transmission to the client interface. The Service Layer, which is the core of the Optimizer System, handles the primary business logic, such as calculating charging schedules, load balancing, and data analysis.

The Charging Point System, in addition to the Communication Layer and Service Layer, incorporates an additional Hardware Layer. The primary role of this layer is to manage hardware devices (such as charging point hardware and sensors) and facilitate communication with them. The integration of the Hardware Layer with other system components is crucial, ensuring that hardware devices function properly and provide real-time feedback. This layer also handles key operations such as switching the charging point on and off, executing charging schedules, and detecting faults.

In the Communication Layer of the Charging Point System, besides basic message reception and parsing capabilities, a \texttt{WebSocket} port has been specifically added. This \texttt{WebSocket} port is designed to support communication with new devices that may be developed in the future. This design enhances the system's scalability, ensuring that future additions of new devices or functionalities will not be restricted by the current communication method.

Additionally, the communication between the two systems is also realized via \texttt{WebSocket} port.

\section{WebSocket}
\label{sec: websocket}

% 得益于全双工通信，\texttt{WebSocket} 允许客户端和服务器同时发送和接收数据，而无需等待对方的响应。与 HTTP 的请求-响应模型不同，\texttt{WebSocket} 连接一旦建立，就可以随时传输数据，从而减少通信延迟。\cite{websockets} \texttt{WebSocket} 连接会一直保持打开状态，直到客户端或服务器主动关闭它。

% 不过，本项目使用上下文管理器自动管理连接，而不是手动打开和关闭连接。\texttt{WebSocket} 端口的打开与关闭过程被封装在 \_\_enter\_\_ 和 \_\_exit\_\_ 方法中，开发者只需使用 with 语句即可确保在进入上下文时自动建立连接，在退出时自动关闭连接并释放资源。(补充：在异步的例子中使用 \_\_aenter\_\_ 和 \_\_aexit\_\_ )这样设计不仅简化了 \texttt{WebSocket} 端口的管理流程，避免了忘记关闭连接或异常退出时资源泄漏的问题，还减少使用try/finally这些语法，增强了代码的可读性和可维护性。

Thanks to full-duplex communication, \texttt{WebSocket} allows the client and server to send and receive data simultaneously without waiting for a response from the other side. Unlike HTTP’s request-response model, once a \texttt{WebSocket} connection is established, data can be transmitted at any time, reducing communication delay\cite{websockets}. The \texttt{WebSocket} connection remains open until either the client or server actively closes it. 

However, instead of manually opening and closing the connection, the context manager is used in this project to automatically manage the connection. The opening and closing process of the \texttt{WebSocket} port is encapsulated in the \texttt{\_\_enter\_\_} and \texttt{\_\_exit\_\_} methods. Developers simply use the \texttt{with} statement; the connection is automatically established upon entering the context and closed upon exiting. And for the asynchronous case, \texttt{\_\_aenter\_\_} and \texttt{\_\_aexit\_\_} are used. And the resources are also released. This design not only simplifies the management process of the \texttt{WebSocket} port, avoids the problem of resource leakage when the connection closure is forgotten or an abnormal exit occurs but also enhances the readability and maintainability of the code.

%To enhance the expansibility and flexibility of the system, this project fully considers the potential need for dynamic opening or closing of \texttt{WebSocket} ports. Especially in real application, \texttt{WebSocket} ports may need to be reconnected, closed, or switched at any time due to various demands or changes in the network environment, for instance, CS must get "Authorize" before charging, but while charging the system accesses "MeterValue". those demands are not taking place at the same time. To make managing the lifecycle of \texttt{WebSocket} ports more convenient and robust, the project introduces a context manager construct to handle the entry and exit of \texttt{WebSocket} connections in general.

%为了提升系统的扩展性和灵活性，本项目设计时充分考虑到\texttt{WebSocket}端口可能存在动态开放或关闭的需求。尤其在实际应用场景中，\texttt{WebSocket} 端口可能因不同业务需求或网络环境的变化而随时进行重连、关闭或切换。为了能够更加方便且安全地管理 \texttt{WebSocket} 端口的生命周期，项目引入了 上下文管理器机制，用于统一管理 \texttt{WebSocket} 连接的进入和退出过程。

%By using a context manager, the process of opening and closing \texttt{WebSocket} ports is encapsulated within the \_\_enter\_\_ and \_\_exit\_\_  methods. Developers can simply use a with statement to ensure that the connection is automatically established when entering the context and properly closed with resources released when exiting. And  for the asynchronous case, \_\_aenter\_\_ and \_\_aexit\_\_ are used. This design not only simplifies the \texttt{WebSocket} port management process and prevents issues like forgetting to close connections or resource leaks in case of unexpected exits but also reduces the need for try/finally statements, improving code readability and maintainability.

%通过使用上下文管理器，\texttt{WebSocket} 端口的打开与关闭过程被封装在 \_\_enter\_\_ 和 \_\_exit\_\_ 方法中，开发者只需使用 with 语句即可确保在进入上下文时自动建立连接，在退出时自动关闭连接并释放资源。(补充：在异步的例子中使用 \_\_aenter\_\_ 和 \_\_aexit\_\_ )这样设计不仅简化了 \texttt{WebSocket} 端口的管理流程，避免了忘记关闭连接或异常退出时资源泄漏的问题，还减少使用try/finally这些语法，增强了代码的可读性和可维护性。

% 26,04评论：可以考虑留一小段简单提一下上下文管理器自动建立和关闭连接，不用太全删，后面的扩展和单例模式那块注释掉
% By applying the context manager, the opening and closing process of the \texttt{WebSocket} port is encapsulated in the \texttt{\_\_enter\_\_} and \texttt{\_\_exit\_\_} methods. Developers simply use the \texttt{with} statement; the connection is automatically established upon entering the context and closed upon exiting. And for the asynchronous case, \texttt{\_\_aenter\_\_} and \texttt{\_\_aexit\_\_} are used. And the resources are also released. This design not only simplifies the management process of the \texttt{WebSocket} port, avoids the problem of resource leakage when the connection closure is forgotten or an abnormal exit occurs, but also enhances the readability and maintainability of the code.

%此外，上下文管理器机制为后续功能扩展提供了良好的基础。例如，未来若需在连接建立或断开时增加日志记录、异常捕获或权限校验等操作，只需在上下文管理器中扩展相应逻辑即可，无需改动主业务流程代码，极大地提高了系统的可扩展性和安全性。

%In addition, the context manager provides a good foundation for subsequent function expansion. For example, if logging, exception handling, or permission verification needs to be added during connection establishment or disconnection, this can simply be achieved by extending the corresponding logic in the context manager without modifying the core logic, which significantly enhances the system's extensibility and security.

%值得一提的是，目前本项目中 \texttt{WebSocket} 端口实例直接组合在 \ac{OCPP} 消息端口类中，存在一定的耦合关系。这种设计方式虽然实现简单、便于快速开发，但从软件架构设计的角度来看，\texttt{WebSocket} 层与\ac{OCPP} 协议层紧密绑定，两者生命周期强相关，不利于后续功能的扩展与维护。

%It is worth mentioning that in this project, the \texttt{WebSocket} port instance is directly integrated in the \ac{OCPP} message port class, and create a certain coupling. This design is simple to implement and facilitates quick development. However, from a software architecture perspective, the \texttt{WebSocket} layer is closely coupled with the \ac{OCPP} protocol layer, and the life cycles of the two are strongly related, which hinders the expansion and maintenance of subsequent functions.

% 个人感觉这里的这里可以提一句：To further decouple the system, some suggestions are offered in \section{Discussion}

%为了解决这个问题，更优雅的设计方式是：单独抽象（用“分离”这个词个人感觉会好些）出\texttt{WebSocket} 端口管理类，采用单例模式实现全局唯一的管理器。管理器内部维护\texttt{WebSocket} 连接池，按\texttt{id}或连接地址、端口进行管理与复用。\ac{OCPP} 协议端口类只需通过管理器获取或注册所需的\texttt{WebSocket} 连接即可，彻底解耦\texttt{WebSocket} 层与\ac{OCPP} 协议解析层，同时提升资源复用率。

%To solve this problem, a more elegant design is to abstract the \texttt{WebSocket} port management into a  class, and use the singleton mode to create the only instance - a globally unique manager.The manager maintains the \texttt{WebSocket} connection pool internally which manages and reuses connection based on connection ID, address and port. The \ac{OCPP} protocol port class only needs to obtain or register the required \texttt{WebSocket} connection through the manager, fully decoupling the \texttt{WebSocket} layer and the \ac{OCPP} protocol parsing layer, while improving the resource reuse rate.

%这里可以放到Disscusion？

\section{Python Library OCPP}
\label{sec: ocppLib}

% OCPP 是由开放充电联盟 (OCA) 开发和维护的协议。在设备管理方面，充电站可以向充电管理系统 (CSMS) 发送详细的诊断数据，从而方便维护。它还利用 ISO 15118 标准进行车辆安全身份验证\cite{OCPP}。由于其良好的兼容性、Python 中现有的库以及其开源协议，所以在本项目中使用 \ac{OCPP} 。在项目启动之初，该协议的最新版本是 2.0.1 版。与 \ac{OCPP} 1.6 相比，\ac{OCPP} 2.0.1 在 JSON 文件中提供了更详细的消息定义、增强了安全功能并提高了兼容性。

% 此外，官方 \ac{OCPP} 库已在 Python 中存在\cite{ocplibrary}。虽然官方库的最新版本是 v2.0.0，但在这个项目开始之前，库的最新版本是 v1.0.0，因此本项目使用 v1.0.0。由于官方库的最新版本发生了重大变化，不再支持旧版本的枚举类。因此，本项目使用的库与最新版本不兼容。

OCPP is a protocol developed and maintained by the Open Charge Alliance (OCA). In terms of device management, charging stations can send detailed diagnostic data to the \ac{CSMS}, facilitating maintenance. It also utilizes ISO 15118 for secure vehicle authentication \cite{OCPP}. \ac{OCPP} is used in this project due to its good compatibility, existing libraries in Python, and its open-source protocol. At the start of this project, Version 2.0.1 was the latest version of the protocol. Compared to \ac{OCPP} 1.6, \ac{OCPP} 2.0.1 offers more detailed message definitions in the JSON files, enhanced security features, and greater compatibility.

 And the official \ac{OCPP} library already exists in Python\cite{ocpplibrary}. Though the latest official version of the library is v2.0.0, but before the start of this project, the latest library version was v1.0.0, that's why this project uses v1.0.0. Due to significant changes in the latest official library, it no longer supports the old version's enumeration classes. Therefore, the library used in this project is not compatible with the latest version.

%OCPP库中包括4个部分，分别为\texttt{ChargePoint}模块，路由（routing）模块，v1.6与v2.0.1的枚举类、数据类等数据定义，以及报错和信息模块。其使用流程为先通过路由模块注册方法，然后启动\texttt{ChargePoint}模块并通过对\texttt{WebSocket}持续监听获取消息，或手动将\texttt{WebSocket}接收的信息传给\texttt{ChargePoint}。注册方法形参是接收的消息，返回值为发送的响应消息。其中注册方法的方式是通过使用\texttt{ocpp.routing}中定义的装饰器\texttt{@on(ocpp.enum.Action) @after(ocpp.enum.Action)}对被注册的函数进行装饰，装饰器是在对应的\texttt{ocpp.enum.Action}中创建注册方法列表，将被装饰的函数名添加其中，随后在\texttt{CP}实例化时，将函数与之绑定。当接收消息并解析时，将执行注册方法列表中绑定的函数。
%该方法的优点在于使用方便，无需额外进行注册的设置或声明，条理清晰，在注册方法定义处即得知其与哪个消息动作绑定。但是该官方库的函数注册实现方式限制了该系统不支持高并发操作,不支持多函数注册以及注册方法必须在\texttt{ocpp.charge\_point.ChargePoint}类中定义。其原理如下:

The \ac{OCPP} library includes 4 parts, namely the \texttt{ChargePoint} module, the \texttt{Routing} module, the enumeration class and data class of v1.6 and v2.0.1, and the error and information module. The procedure is to first register the method through the routing module, then start the \texttt{ChargePoint} module and obtain messages by continuously listening to \texttt{WebSocket}, or manually pass the information received by \texttt{WebSocket} to \texttt{ChargePoint}. The formal parameter of this registration method is the received message, and the returned value is the sent response message. The registration method is to decorate the registered function by using the decorators \texttt{@on(ocpp.enum.Action)} and \texttt{@after(ocpp.enum.Action)} defined in \texttt{ocpp.routing}. The decorator creates a registration method list in the corresponding \texttt{ocpp.enum.Action}, adds the decorated function name into it, and then binds the function to it when \texttt{ChargePoint} is instantiated. When the message is received and parsed, the bound function in the registration method list will be executed.
The advantage of this method is that it is easy to use, requiring no additional registration settings or declarations. It is well-organized, and the message action to which the registration method is bound can be easily identified in the method definition. 

However, the official library's function registration implementation method has several limitations:
\begin{enumerate}
    \item no support for high-concurrency operations
    
    In the code \texttt{ChargePoint.\_handle\_call(self, msg)}, when the code tries to get the method registered with \texttt{@on}, it applies directly bound using a dictionary mapping. When the first message is being processed by the registered method and a second message with the same action is received, the second message has to wait for the first one to finish processing before it can be handled. As a result, when multiple clients send the same request, the system may experience a response timeout due to its inability to process subsequent messages in time. 
    
    However, modifying the \ac{OCPP} library could introduce potential errors and increase the difficulty of porting the code to other devices, so we chose not to modify the library. Instead, we propose two possible solutions:
    
    \begin{itemize}
        \item %对库的注册结构进行更改，不修改传递消息的格式。可以在\texttt{@on}注册方法时，注册一个工厂，当接收到消息后，应该由工厂生产方法，然后执行生产出的方法，而非工厂函数，这样就将消息传入和执行进行了分离解耦，然后将被执行的方法加上时间戳，放入执行队列中，使用另一个对象对队列进行监听。如果超时，则强制中断方法的执行，销毁方法对象并移出队列，同时返回超时的信号，当列表为空时则停止监听。这样通过动态生成、管理执行对象就实现了对同时接收多个同消息动作的消息处理的支持。

        Change the registration structure of the library without modifying the format of the message transmission. 
        Register a factory when registering a method in \texttt{@on}. When a message is received, the factory should produce a method and then execute the produced method instead of the factory function. This separates and decouples the message input and execution. Then add a timestamp to the executed method, put it in the execution queue, and use another object to monitor the queue. If a timeout occurs, the execution of the method is forced to be interrupted, the method object is destroyed and removed from the queue, and a timeout signal is returned. When the list is empty, the listening will be stopped. In this way, by dynamically generating and managing execution objects, support for message handling when receiving multiple messages with the same action at the same time is achieved.
        
        \item %对库的注册结构进行更改，同时修改传递消息的格式。不使用装饰器的方式注册方法，而是使用信号(\autoref{sec:signal})对其连接，同第一种方法一样分离处理消息和接收消息的动作，然而需要再请求端发送时同时数据的发送时间戳，然后将执行方法加入队列，启动监听循环，当消息超时，则移出队列，并反馈/报错消息超时。与第一种方法的不同点在于，使用信号可以同时解决不能对一个动作注册多个方法的问题

        Change the registration structure of the library and modify the format of the message transmission. Instead of using decorators to register methods, it is also possible to use signals (\autoref{sec: signal}) to connect them. Like the first approach, this separates the actions for handling and receiving messages. However, it requires the sender to send a timestamp with the data. Then add the execution method to the queue and start the listening loop. If a message times out, it is removed from the queue, and a timeout error is returned. The difference from the first method is that using signals can solve the problem of not being able to register multiple methods for one action at the same time.
        
    \end{itemize}
    
    \item no support for multi-function registration
    
    The code \texttt{ocpp.routing.create\_route\_map(obj)} uses a dictionary to define the mapping of the registration method. However, since the direct assignment method \texttt{routes[action][option] = attr} is used, when a function is registered with the decorator of the same message action at the same time, for example \texttt{@on(Action.authorize)}, the function decorated later will overwrite the function decorated earlier. Therefore, it does not support registering multiple functions to handle the same message action.
    
    \item all registered methods must be defined within the \texttt{ocpp.charge\_point.\\ChargePoint} class

    The code \texttt{ocpp.routing.create\_route\_map(obj)} uses the \texttt{getattr(obj, attr\_name)} method to obtain the registration method, and when instantiated in \texttt{ChargePoint}, the parameter passed to \texttt{routing.create\_route\_map(obj)} is \texttt{self}, that is, \texttt{ChargePoint} itself, so when the registration method is defined in other non-\texttt{ChargePoint} classes and their subclasses, it will not be registered, and the function will not be called for processing when receiving related message actions. Therefore, the registration method definition is strictly limited to the \texttt{ocpp.charge\_point.ChargePoint} class.
\end{enumerate}
%The reason is as follows:
%\begin{itemize}
    %\item %代码行%\texttt{ocpp.charge\_point.ChargePoint.\_handle\_call(self, msg), line 284}中获取被\texttt{@on}注册的方法时，使用的是字典的映射来直接绑定的。当调用注册方法处理第一个消息时，如果此时传进第二个相同消息动作的消息，则第二个消息只能等待第一个消息处理完才能被接着处理。这样当存在多客户端发送相同请求时，系统可能会因为无法处理后续消息而导致响应超时。然而由于需要更改ocpp库，考虑到代码可能增加移植在别的设备的难度，项目中我们并未对库进行修改，但我们提出了两个可能的解决方法：

   % In the code \texttt{ChargePoint.\_handle\_call(self, msg)}, when the code trying to get the method registered with \texttt{@on}, it applies directly bound using a dictionary mapping. When the first message is being processed by the registered method and a second message with the same action is received, the second message has to wait for the first one to finish processing before it can be handled. As a result, when multiple clients send the same request, the system may experience a response timeout due to its inability to process subsequent messages in time. 
    
    %However, modifying the \ac{OCPP} library could introduce potential errors and increase the difficulty of porting the code to other devices, so we chose not to modify the library. Instead, we propose two possible solutions:
    
    %\begin{itemize}
        %\item %对库的注册结构进行更改，不修改传递消息的格式。可以在\texttt{@on}注册方法时，注册一个工厂，当接收到消息后，应该由工厂生产方法，然后执行生产出的方法，而非工厂函数，这样就将消息传入和执行进行了分离解耦，然后将被执行的方法加上时间戳，放入执行队列中，使用另一个对象对队列进行监听。如果超时，则强制中断方法的执行，销毁方法对象并移出队列，同时返回超时的信号，当列表为空时则停止监听。这样通过动态生成、管理执行对象就实现了对同时接收多个同消息动作的消息处理的支持。

        %Change the registration structure of the library without modifying the format of the message transmission. 
        %Register a factory when registering a method in \texttt{@on}. When a message is received, the factory should produce a method and then execute the produced method instead of the factory function. This separates and decouples the message input and execution. Then add a timestamp to the executed method, put it in the execution queue, and use another object to monitor the queue. If a timeout occurs, the execution of the method is forced to be interrupted, the method object is destroyed and removed from the queue, and a timeout signal is returned. When the list is empty, the listening will be stopped. In this way, by dynamically generating and managing execution objects, support for message handling when receiving multiple messages with the same action at the same time is achieved.
        
        %\item %对库的注册结构进行更改，同时修改传递消息的格式。不使用装饰器的方式注册方法，而是使用信号(\autoref{sec:signal})对其连接，同第一种方法一样分离处理消息和接收消息的动作，然而需要再请求端发送时同时数据的发送时间戳，然后将执行方法加入队列，启动监听循环，当消息超时，则移出队列，并反馈/报错消息超时。与第一种方法的不同点在于，使用信号可以同时解决不能对一个动作注册多个方法的问题

        %Change the registration structure of the library and modify the format of the message transmission. Instead of using decorators to register methods, it is also possible to use signals (\autoref{sec: signal}) to connect them. Like the first approach, this separates the actions for handling and receiving messages. However, it requires the sender to send a timestamp with the data. Then add the execution method to the queue and start the listening loop. If a message times out, it is removed from the queue, and a timeout error is returned. The difference from the first method is that using signals can solve the problem of not being able to register multiple methods for one action at the same time.
        
    %\end{itemize}  
    
    %\item %代码行\texttt{ocpp.routing.create\_route\_map(obj)，line 134}中使用字典定义了注册方法的映射，然而由于使用的是\texttt{routes[action][option] = attr}直接赋值的方式，会导致同时被相同消息动作的装饰器装饰注册时,例如\texttt{@on(Action.authorize)},后被装饰的函数将覆盖之前装饰的函数，因此不支持注册多函数处理同一个消息动作。

    %The code \texttt{ocpp.routing.create\_route\_map(obj)} uses a dictionary to define the mapping of the registration method. However, since the direct assignment method \texttt{routes[action][option] = attr} is used, when a function is registered with the decorator of the same message action at the same time, for example \texttt{@on(Action.authorize)}, the function decorated later will overwrite the function decorated earlier. Therefore, it does not support registering multiple functions to handle the same message action.
    
    %\item %代码行\texttt{ocpp.routing.create\_route\_map(obj)，line 120}中使用了\texttt{attr = getattr(obj, attr\_name)}方法获取注册方法，而在\texttt{ChargePoint}中实例化时，向\texttt{ocpp.routing.create\_route\_map(obj)}传入的参数为self,即\texttt{ChargePoint}本身，所以当注册方法被定义在其他非\texttt{ChargePoint}类及其子类中时，将不会被注册，接收到相关消息动作时将不会调用函数进行处理。因此注册方法定义被严格限制在\texttt{ocpp.charge\_point.ChargePoint}类中。

   % \item The code \texttt{ocpp.routing.create\_route\_map(obj)} uses the \texttt{getattr(obj, attr\_name)} method to obtain the registration method, and when instantiated in \texttt{ChargePoint}, the parameter passed to \texttt{routing.create\_route\_map(obj)} is \texttt{self}, that is, \texttt{ChargePoint} itself, so when the registration method is defined in other non-\texttt{ChargePoint} classes and their subclasses, it will not be registered, and the function will not be called for processing when receiving related message actions. Therefore, the registration method definition is strictly limited to the \texttt{ocpp.charge\_point.ChargePoint} class.    
%\end{itemize}

\section{Method to get OCPP data}
\label{sec:ocppSendReceive}
% \ac{OCPP}官方库中给出的获取数据方式是通过对方法进行注册，在注册方法的形参中获取消息的一级键名，而这些形参在接受消息时会被自动解包赋值，于是就得到了对一层json数据的展开数据。而发送响应则是在注册方法中返回包含响应数据的指定的数据类。
% 然而该方法存在接收消息，处理消息，返回消息的耦合，当情况复杂时代码难以扩展。为了对该方法进行解耦，本项目将使用信号\autoref{sec:signal}分离接收的消息，OCPP消息信号一共有三种:

In the \ac{OCPP} official library, data is obtained by registering a method, where the first-level key name of the message is passed as a parameter to the registration method. These parameters are automatically unpacked and assigned when the message is received, providing the expanded data of one layer of JSON. To send a response, the registration method returns a data class containing the response data.
However, this method couples the receiving, processing, and returning of messages, making it difficult to extend when the situation becomes more complex. To decouple this process, this project will use signals (see \autoref{sec: signal}) to separate the message reception. There are three types of \ac{OCPP} message signals (\autoref{fig:signalMsgCommunication}):

\begin{itemize}
    %\item \texttt{signal\_request} 用于接收传递请求方发来的请求信息，信号的具体内容为包含时间戳，消息动作，消息id，以及消息内容的一个字典
    %\item \texttt{signal\_response} 用于接收传递接收方发来的响应信息，信号的具体内容为包含消息动作，请求消息，响应消息，请求消息的时间戳，响应消息有效性的状态(成功收到响应，响应超时，接收错误)的一个字典。当请求发送方，等待响应消息超时时，将自动接收到一个含有响应消息有效性状态为响应超时的信号数据。
   % \item \texttt{signal\_response\_result} 用于传递接收方发送响应消息后的结果，信号具体内容为包含消息动作，请求消息的时间戳，响应消息，发送结果(在有效时间内成功发送响应，超时发送，发送错误)的一个字典。由于请求消息发送后一定会有响应消息返回，但是响应消息发送后，系统难以知道是否在规定时间内返回了响应消息。于是基于系统中的自查，将对响应消息的结果进行反馈。此信号可以用于对某些固定数据进行缓存处理，当出现高频的请求时，可以直接使用上一次未成功发送的数据，减少计算时间。然而本项目暂时没有高频请求的需求，故只创建了信号，未使用该信号。

    \item \texttt{signal\_request} is used to receive the request information sent by the requester. The specific content of the signal is a dictionary containing the timestamp, the message action, the message ID, and the message content. 
    \item \texttt{signal\_response} is used to receive the response information sent by the receiver. The specific content of the signal is a dictionary containing message action, request message, response message, timestamp of request message, and status of response message validity (successful response received, response timeout, reception error). When the request sender times out while waiting for a response message, a signal data containing the response message validity status of the response timeout will be automatically received. 
    \item \texttt{signal\_response\_result} is used to transmit the result after the receiver sends a response message. The specific content of the signal is a dictionary containing message action, timestamp of request message, response message, and sending result (successful response sent within the valid time, timeout sending, sending error). After a request message is sent, a response message will be returned. However, after the response message is sent, it is difficult for the system to know whether the response message is returned within the specified time. Therefore, based on the self-check in the system, the result of the response message will be fed back. This signal can be used to cache certain fixed data. When there are high-frequency requests, the data that was not successfully sent last time can be used directly to reduce the calculation time. However, this project does not have the need for high-frequency requests for the time being, so only the signal is created and not used.
\end{itemize}
\begin{figure}[H]
    \centering
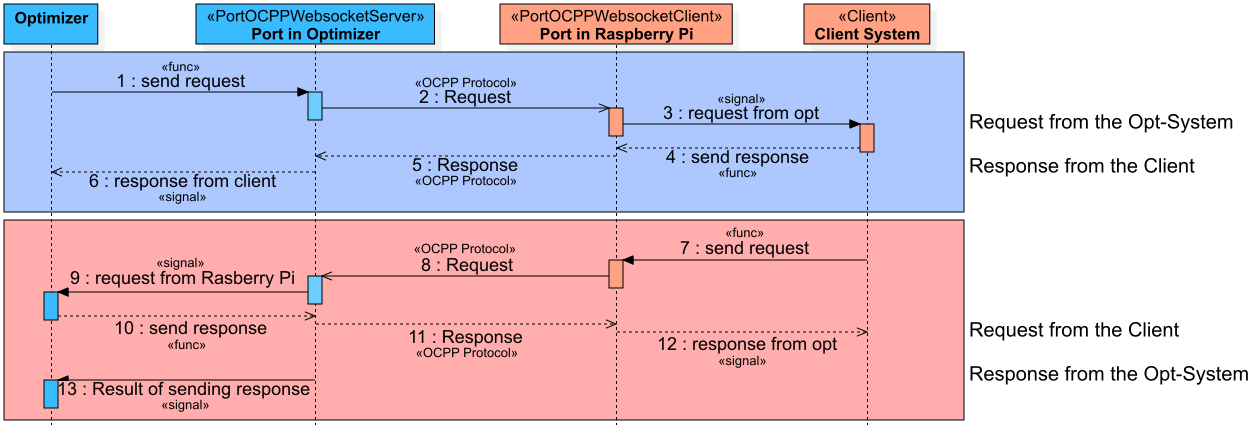
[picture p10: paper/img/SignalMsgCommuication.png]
    
    \caption{Message Communication}
    \label{fig:signalMsgCommunication}
\end{figure}

% 而发送OCPP数据则是通过手动调用\texttt{send\_response\_message}与\texttt{send\_request\_message}方法发送数据，分离了接收请求消息与发送响应消息的关系。

% 由于该项目未改变原来ocpp库的代码，所以仍是通过注册获取信息，然而注册方法的返回则是调用一个\texttt{while}循环方法，该方法中循环监听响应消息队列，并检查时间是否超时。当消息队列存在消息时，退出循环并返回消息给注册方法，注册方法返回响应消息，通过\texttt{ChargePoint}类发送响应消息。其中消息队列用于隔离同步与异步程序，同时支持多消息排队等候发送。检查时间可以设置预估网络延迟时间和提前发送时间，例如标准timeout为30s，预估网络延迟为5s，提前发送时间为1s，则实际允许等待的时间为24s，超时则将自动返回默认消息，同时向系统反馈超时发送。

Since the original \ac{OCPP} library code is not modified in this project, information is still obtained through registration. However, the return of the registration method is to call a \texttt{while} loop method, which loops to listen to the response message queue and checks whether a timeout occurs. When there is a message in the message queue, the program will exit the loop and return the message to the registration method. The registration method returns the response message and sends the response message through the \texttt{ChargePoint} class. The message queue is used to isolate synchronous and asynchronous programs, and supports multiple messages waiting to be sent in the queue. The check time can set the estimated network delay time and the advanced sending time. For example, the standard timeout is 30s, the estimated network delay is 5s, and the advance sending time is 1s. The actual waiting time allowed is 24s. If the timeout exceeds, the default message will be automatically returned, and the timeout will be fed back to the system.

\section{Method to generate OCPP data}
\label{sec:ocppGenerator}
% 相对于层级结构简单，最大层级仅有两层的ocpp 1.6 的消息格式，ocpp 2.0.1的消息格式在结构上则显著复杂得多，消息的层级更深且不固定，甚至存在4层以上的复杂层级关系。虽然现有的 OCPP 库中提供了相应的消息数据类用于封装消息内容，但在实际编码过程中，开发者仍然需要手动对这些数据类赋值或直接构造复杂的嵌套字典结构。这种手动构建消息的方式存在显著的风险和问题。首先，由于 OCPP 2.0.1 中的数据字段极为丰富，字段之间存在大量的类型约束、必填与选填的限制关系，以及嵌套结构的要求，开发者在手动构建过程中极易因疏忽而填错字段、遗漏关键参数或违反字段约束，进而导致 OCPP 消息在传输过程中被拒绝或通信失败。其次，开发者在面对庞大的协议标准时，往往需要频繁查阅官方 JSON Schema 或文档，以确认字段名称、数据类型及其含义，增加了开发成本，降低了开发效率。
% 为了解决上述问题，降低 OCPP 消息构建过程中的出错概率，并提升开发效率，本项目设计并实现了一种参考于建造者模式思想，且充分发挥IDE的DocString提示功能的ocpp消息生成器用来创建ocpp消息。生成器的核心思想是将 OCPP 消息的复杂结构封装在函数接口中，开发者无需关注底层的嵌套关系和字段约束，仅需按照函数的参数提示逐级调用并完成数据填充即可自动生成符合 OCPP 协议标准的数据类或字典。

Compared with the message format of \ac{OCPP} 1.6, which has a simple hierarchical structure and only two layers at the maximum, the message format of \ac{OCPP} 2.0.1 is significantly more complex in structure. The message hierarchy is deeper and not fixed, and sometimes exceeds four layers. Although the existing \ac{OCPP} library provides corresponding message data classes for encapsulating message content, in the actual coding process, developers still need to manually assign values to these data classes or directly construct complex nested dictionary structures. This manual approach introduces significant risks and challenges. First, due to the extremely rich data fields in \texttt{OCPP 2.0.1}, there are a large number of type constraints, mandatory and optional restrictions between fields, and nested structure requirements. Developers are very likely to fill in the wrong fields, omit key parameters, or violate field constraints due to negligence during the manual construction process, which will cause \ac{OCPP} messages to be rejected or communication fail during transmission. Secondly, when facing a large number of protocol standards, developers often need to frequently refer to the official JSON Schema or documents to confirm the field name, data type and its meaning, which increases development costs and reduces development efficiency. 

In order to solve the above problems, reduce the error probability in the process of building \ac{OCPP} messages, and improve development efficiency, this project designed and implemented an \ac{OCPP} message generator that refers to the builder pattern\cite{DesignPatterns} and fully utilizes the \texttt{DocString} prompt function of the IDE to create \ac{OCPP} messages. The core idea of the generator is to encapsulate the complex structure of the \ac{OCPP} message in the function interface. Developers only need to follow level-by-level prompts to fill in the data, automatically generating a data class or dictionary that conforms to the \ac{OCPP} protocol standard, without worrying about the underlying nested structures or field constraints.

% 具体而言，OCPP 消息生成器以函数的形式存在，函数的形参即为单层数据的各个字段名，实参则为对应的字段值。函数内部根据 OCPP 协议的定义自动完成数据的封装和结构构建，最终返回符合标准的数据对象。由于生成器函数配备了完善的类型注解和文档字符串，开发者在使用主流 IDE编写代码时，IDE 能够自动识别函数的参数类型、限制条件及字段描述，直接在代码编辑过程中给予开发者完整的提示和校验，大大降低了开发门槛和出错概率。

Specifically, the \ac{OCPP} message generator exists in the form of a function. The formal parameters of the function are the field names of the single-layer data, and the actual parameters are the corresponding field values. The function automatically completes the encapsulation and structure construction of the data according to the definition of the \ac{OCPP} protocol, and finally returns a data object that meets the standard. Since the generator function is equipped with complete type annotations and document strings, when developers use mainstream IDEs to write code, the IDE can automatically identify the function's parameter type, restrictions, and field descriptions, and directly provide developers with complete prompts and verification during the code editing process, greatly reducing the development threshold and error probability.

% 与传统手动构建消息或查阅 JSON Schema 文件的方式相比，OCPP 消息生成器具备以下优势：
% \begin{itemize}
%     \item 开发者无需反复查阅协议文档或 JSON 文件即可快速生成完整的 OCPP 消息
%     \item 通过类型提示和 IDE 自动补全功能，有效避免字段拼写错误、数据类型错误或结构不匹配问题
%     \item 生成器函数具备清晰的层次和注释，后续协议更新时可自动重新生成，提高项目的可维护性和扩展性
%     \item 生成的代码结构清晰，易于阅读和理解，降低团队沟通成本
% \end{itemize}

Compared with the traditional way of manually building messages or consulting JSON Schema files, the \ac{OCPP} message generator has the following advantages:
\begin{itemize}
    \item Developers can quickly generate complete \ac{OCPP} messages without repeatedly consulting protocol documents or JSON files.
    \item Type hints and IDE auto-completion functions can effectively avoid field spelling errors, data type errors, or structure mismatches.
    \item The generator function has a clear hierarchy and comments, and can be automatically regenerated when the protocol is updated later, improving the maintainability and scalability of the project.
    \item The generated code has a clear structure, is easy to read and understand, and reduces team communication costs.
\end{itemize}

% 值得一提的是，考虑到 OCPP 协议中消息种类繁多、结构复杂，本项目并未手动逐条编写生成器函数，而是设计了一套自动化脚本。该脚本能够直接读取 OCPP 官方发布的 JSON Schema 文件，解析各个消息的字段定义、嵌套关系和数据类型，进而自动批量生成对应的 Python 消息生成器函数。最终，项目共计生成了 206 个 OCPP 消息生成器函数，完整覆盖 OCPP 2.0.1 协议中的所有消息类型，极大提升了开发效率和系统的完整性，对于刚刚发布的OCPP 2.1，尽管OCPP库开发人员对其中的枚举类进行了重构，但只需对生成脚本中的枚举名称适配规则进行简单修改，便可直接支持新的协议版本，无需从零开始重新开发。

It is worth mentioning that, considering the wide variety and complex structure of messages in the \ac{OCPP} protocol, this project did not manually write generator functions one by one, but designed a set of automated scripts. This script can directly read the JSON Schema file officially released by \ac{OCPP}, parse the field definition, nested relationship and data type of each message, and then automatically generate the corresponding Python message generator functions in batches. In the end, the project generated a total of 206 \ac{OCPP} message generator functions, which fully covered all message types in the \ac{OCPP} 2.0.1 protocol, greatly improving development efficiency and system integrity. For the newly released \ac{OCPP} 2.1, although the \ac{OCPP} library developers have refactored the enumeration class, only minor adjustments to the enumeration name adaptation rules in the generated script are required to support the new protocol version, eliminating the need for redevelopment from scratch.

\section{Signal}
\label{sec: signal}

% 信号和槽函数最初在 Qt 框架中引入，旨在降低不同系统模块之间的耦合度。Qt 是由 Qt 公司设计的跨平台框架，它简化了 \ac{GUI} 的构建\cite{Qt}。在本项目中，我们利用了信号和槽函数机制，该机制允许组件之间互不依赖地进行交互。一个信号可以连接到多个槽函数，而一个槽函数也可以连接到多个信号，从而使系统更加灵活。

% 由于这种结构是事件驱动的，因此非常适合处理事件并执行相应的代码逻辑。与回调函数相比，信号允许动态地连接和断开槽函数，而回调函数必须事先定义。因此，在执行过程中无法修改回调函数的调用。然而，由于信号与槽函数是动态连接的，因此显式地检查信号连接可能具有挑战性，尤其是在信号连接的定义分布在不同的类或模块中时。因此，在出现错误时跟踪函数和方法的调用变得非常困难。

The Signal and Slot was first introduced in the Qt framework to reduce coupling between different system modules. Qt is a cross-platform development toolkit, designed for creating both \ac{GUI} and non-\ac{GUI} applications \cite{Qt}. In this project, we take advantage of the Signal and Slot mechanism, which allows components to interact without relying on each other. A single signal can be connected to multiple slot functions, while a single slot function can also be connected to multiple signals, making the system more flexible.

Compared to callback functions, signals allow dynamic connections and disconnections of slot functions, whereas callbacks must be defined beforehand, making it impossible to modify their calls during execution. However, signals connect to slot functions dynamically, it can be challenging to explicitly check signal connections, especially when the definitions of signal connections are distributed across different classes or modules. Thus, tracking calls of functions and methods becomes very difficult during the occurrence of bugs.

% 本项目借鉴与于Qt的信号槽机制，基于观察者模式，自行设置实现此机制。由于该系统无需图形界面，同时尽可能降低内存的使用，所以没有使用qt中的信号槽系统。本项目的信号的执行方式为同步执行，不支持异步执行，由于信号实现不基于\texttt{QObject}或者Qt的元对象系统，信号实例化所在的类无需继承某个特定的类，所以在访问数据时，尤其是线程，可能存在数据安全问题，造成数据不一致。但由于该系统较小，涉及共享数据部分很少，该问题可以视为影响很小。当信号在线程中激活时，即使槽函数是在主进程中定义的，槽函数也仍将在线程中运行。即使相比于Qt的信号槽系统，该槽函数无需使用装饰器进行注册，同时信号无需在\texttt{QObject}中实例化，支持类信号和实例信号。

This project adapts the signal-slot mechanism from Qt, based on the observer pattern \cite{DesignPatterns}, to implement its own version. Since the system does not require a graphical interface and aims to minimize memory usage, the Qt signal-slot system is not used. The signals in this project are executed synchronously and do not support asynchronous execution. Unlike Qt's implementation, the signals here are not based on \texttt{QObject} or Qt's meta-object system, meaning the class containing the signal does not need to inherit from any specific class. As a result, while accessing data, especially in multi-threaded scenarios, there may be data safety concerns, leading to potential inconsistencies. However, given the system's small size and the limited shared data, this issue can be considered to have little impact. When a signal is activated within a thread, even if the slot function is defined in the main process, the slot will still execute within the thread. Unlike Qt’s signal-slot system, this implementation does not require decorators for registration, supports both class-level and instance-level signals and signals do not need to be instantiated in \texttt{QObject}.

% 本项目中信号使用了两种方法进行实现。

In this project, signals are implemented using two methods.
\begin{itemize}
    % \item 第一种是简单的实现模式，在信号类中，创建一个槽函数列表，其用于在\texttt{connect()}方法中注册槽函数，同时也可以在\texttt{disconnect()}中注销槽函数，当信号使用\texttt{emit}进行激活时，将逐个向槽函数列表中的槽函数传参并执行，执行顺序为\texttt{connect()}的连接顺序，如果其中一个槽函数阻塞进程，则后续的槽函数也将被阻塞执行，直至该槽函数停止阻塞，并结束执行。该方法的好处在于实现方法很简单，不涉及特殊的python机制，但存在覆盖赋值的问题，如果要安全使用信号，则需要在类内使用私有属性定义信号，并使用\texttt{@property}提供访问方法，这样将阻止意外对信号进行赋值而发生错误，但仅限于实例信号，类信号仍存在覆盖赋值问题。

    \item The first implementation is a simple approach. In the signal class, a slot function list is created to store registered slot functions via the \texttt{connect()} method. At the same time, the slot function can also be unregistered in \texttt{disconnect()}. When the signal is triggered with \texttt{emit()}, the provided parameters are passed to all registered slot functions. These functions are executed sequentially in the order they were connected via \texttt{connect()}. If one of the slot functions blocks execution, the subsequent slot functions will also be blocked until the slot function stops blocking and ends execution. The advantage of this method is its simplicity - it does not involve special Python mechanisms, it has a potential issue of overwriting assignment. To ensure safe usage, signals should be defined as private attributes within a class and exposed via \texttt{@property} methods. This prevents accidental overwrites but is limited to instance-level signals. Class-level signals still face the risk of being overwritten due to direct assignment.
    
    % \item 第二种方法是使用python的描述符\texttt{\_\_get\_\_}, \texttt{\_\_set\_\_}，通过工厂模式返回真实连接信号。其优点在于只需定义一次，无需使用私有属性和\texttt{@property}进行保护，可以在\texttt{\_\_set\_\_}中对信号禁用赋值，该保护对类信号仍有效，同时可以通过工厂对该类下所有的信号进行管理，在调试过程中可以通过工厂的信号列表，查看所有信号和所连接的槽函数，其缺点则是实现较为复杂，需要使用特殊方法\texttt{\_\_set\_\_}, \texttt{\_\_get\_\_}等，由于需要将信号和类做绑定，所以需要再类中创建保存所有信号实例的列表，因此对于某些严格限制类/实例属性的类并不兼容。

    \item The second method utilizes Python’s descriptor methods, \texttt{\_\_get\_\_} and \texttt{\_\_set\_\_}, to return the actual signal connection through the factory pattern. The factory pattern is a design pattern that creates objects through a factory class, which returns different types of objects based on input parameters, without the need for the client code to directly specify the concrete class \cite{DesignPatterns}. Its advantage is that it only needs to be defined once, without the need to use private attributes and \texttt{@property} for protection. Additionally, the signal assignment can be disabled in \texttt{\_\_set\_\_}, which is still valid for class signals. Furthermore, all signals under the class can be managed through the factory. During debugging, all signals and connected slot functions can be viewed through the factory's signal list. However, this approach is more complex, requiring the use of special methods such as \texttt{\_\_set\_\_} and \texttt{\_\_get\_\_}. Since signals needs to be bound to the class, a list of all signal instances needs to be created in the class. This makes it not compatible with certain classes that strictly restrict class/instance attributes.
    
\end{itemize}
% 两种方法都可以在信号初始化时限制信号传参类型，例如信号只允许两个参数传入，\texttt{int|str，list}。当信号调用 \texttt{emit()} 传入其他不符合定义类型的数据时，将对其报错，降低由于类型不明确而意外产生错误的可能性。

Both methods allow restricting the signal’s parameter types during initialization. For example, a signal can be defined to accept only two parameters (\texttt{int|str, list}). If \texttt{emit()} is called with arguments that do not conform to the specified types, an error will be raised, minimizing the risk of unintended type-related errors.

% 在\autoref{sec:ocppLib}中介绍了ocpp库的调用方式，这种装饰器方法使得执行方法必须定义在\texttt{ocpp.ChargePoint}类中，这就导致ChargePoint不仅需要分发传进来的消息，同时也要执行相应的处理逻辑。这样就要求执行实例必须定义在ChargePoint中，意味着ChargePoint类是一个顶层或者较为上层的类，然而实际上可能存在同级跨类调用或多进程/线程执行，这样将使得ChargePoint类非常大，且违反了单一职能原则。例如优化器计算模块可以定义为线程，并等待数据的传入，该线程不应与ChargePoint的生命周期绑定，而应该独立存在。
% 所以需要对ChargePoint类的功能进行拆解，使ChargePoint仅是对消息进行拆包解析，在逻辑层或更高层级的类中进行分包和执行。这样就实现了WebSocket进行收发消息，ChargePoint进行消息解包分析，更高一级的类进行消息分发，并支持跨类调用。这样则降低了系统模块间的耦合度，并且保证了单一职能原则，同时也支持了对多端口多进程的扩展开发可能性，提高了扩展能力。所以决定使用信号槽机制来进行系统内通讯。

The calling method of the \ac{OCPP} library is introduced in \autoref{sec: ocppLib}. This decorator method requires the execution methods to be defined in the \texttt{ocpp.ChargePoint} class, which means that ChargePoint not only needs to distribute the incoming messages, but also needs to execute the corresponding processing logic. This requires that the execution instance must be defined in ChargePoint, which means that the ChargePoint class is a top-level or upper-level class. However, in practice, there may be same-level cross-class calls or multi-process/thread execution, which will make the ChargePoint class very large and violate the single responsibility principle. For example, the optimizer calculation module can be implemented as a separate thread that passively waits for incoming data. This thread should exist independently rather than being bound to the lifecycle of ChargePoint. 

Therefore, it is necessary to decouple the responsibilities of the ChargePoint class so that ChargePoint only unpacks and parses the message. The distribution of messages and execution of command will be completed in the logical layer or higher-level classes. Under this design, WebSocket handles message transmission, ChargePoint processes message unpacking and analysis, and an upper-layer class manages message distribution, allowing for cross-class calls. This reduces the coupling between system modules and adheres to the Single Responsibility Principle. It also supports the possibility of extended development of multi-port and multi-process, and improves the expansion capability. Therefore, the signal-slot mechanism is adopted for internal communication within the system.

\section{Asynchronous Isolation}
\label{sec: asyncIsolation}

% 一个进程可以拥有多个线程，线程用于在单个程序中执行多个并发（假设 CPU 只有一个核心）或并行（假设 CPU 有多个核心）操作。与线程不同，协程允许暂停和恢复执行。如表 \autoref{tab:threadandcoroutine} 所示，协程在执行不同任务时无需切换上下文，或者切换上下文的代价较低。上下文是指程序在特定时刻的执行状态，包括寄存器信息、调用堆栈、内存数据等。当 CPU 在不同任务（线程、进程或协程）之间切换时，需要保存当前任务的状态并恢复下一个任务的状态，以确保程序的连续执行\cite{coroutinetutorial}。

A process can have multiple threads, and threads are used to execute multiple concurrent (assuming that the CPU has one core) or parallel (assuming that the CPU has multiple cores) operations within a single program. Different from threads, coroutines allow execution to be suspended and resumed. As shown in \autoref{tab: threadandcoroutine}, while executing different tasks, coroutines don't need to switch the context or with a low switching-context cost. Context refers to the execution state of a program at a given moment, including register information, the call stack, memory data, and so on. When the CPU switches between different tasks (threads, processes, or coroutines), it needs to save the current task's state and restore the next task's state to ensure continuous execution \cite{coroutinetutorial}.

\begin{table}[htbp]  
  \centering        
  \begin{tabular}{|l|c|c|}
    \hline
    \textbf{Characteristic} & \textbf{Multi-Thread} & \textbf{Coroutine}\\
    % \hline
    % Blocking & No & No\\
    \hline
    Switching context cost & High & Low\\
    \hline
    Memory usage & High & Low\\
    \hline
    Execution Modes & Concurrency / Parallelism & Concurrency\\
    \hline
    Execution Layer & Kernel Mode & User Mode\\
    \hline
    Scheduler & Operating System Scheduler & Self-Scheduling by Programs\\
    \hline
  \end{tabular}
  \caption{Comparison between Thread and Coroutine}
  \label{tab: threadandcoroutine}
\end{table}

% 频繁的 I/O 操作是指程序在执行过程中频繁地读写数据，而不是持续地进行计算。在汽车充电的场景中，充电站的计算需求并不高，而是需要频繁地读取命令。从表中可以看出，协程是非阻塞的，这避免了在频繁的 I/O 操作期间 CPU 被占用但未被充分利用的情况。因此，在这种场景下，协程比线程更合适。

 % Frequent I/O operations mean that during execution, a program frequently reads or writes data rather than continuously calculating. In the case of vehicle charging, the computational demand of charging stations is not high; instead, they require frequent command reading. From the table, we can see that coroutines are non-blocking, which prevents situations where the CPU is occupied but not actively utilized during frequent I/O operations. Therefore, in such scenarios, coroutines are more suitable than threads. 

%这里如果要进一步说明thread在执行顺序上的区别 可以加入thread coroutine的时序图并且语言简单描述下 ？

% 需要注意的是，如果函数内部使用了“await”语法，则必须将其声明为“async”，因为“await”只能在协程函数中使用。调用此异步函数的上级函数也必须使用 await 来等待其结果，这意味着上级函数也必须变为异步函数。换句话说，async 和 await 总是成对出现，它们可以强制将原本不需要异步操作的函数也修改为异步函数。然而大多数传统程序是以同步编程为主，异步模式的大量引入不仅加大了代码的管理和维护难度，还会降低程序的可扩展性和可读性，导致原本清晰的同步调用链变得复杂且难以追踪。因此，将异步程序与同步程序隔离是非常必要的。 

It is important to note that if a function uses the "await" syntax inside, it must be declared as "async" because "await" can only be used within a coroutine function. The higher-level function that calls this async function must also use await to wait for its result, which means the higher-level function must also become async. In other words, async and await always appear in pairs, and they can force functions that initially do not require asynchronous operations to be modified into asynchronous functions as well. However, most traditional programs are based on synchronous programming. The large-scale introduction of asynchronous modes not only increases the difficulty of code management and maintenance but also reduces the scalability and readability of the program, causing the originally clear synchronous call chain to become complicated and difficult to trace. Therefore, it is very necessary to isolate asynchronous components from synchronous programs.

% 由于本项目中使用\texttt{WebSocket}模块，而\texttt{WebSocket}模块本身是基于异步机制实现的，涉及的所有方法调用均为异步函数（async 方法），因此包含\texttt{WebSocket}交互的模块，如\texttt{ChargePoint}类，均被划分为异步编程模块。而其他部分如数据处理、业务逻辑以及控制流程仍然采用同步编程模式，保持传统同步调用的清晰性和直观性。为了隔离这两种编程模式，本项目借鉴了生产者消费者设计模式，同时通过信号进行数据传递。生产者消费者模式将生产者和消费者解耦，使它们各自独立运行，并通过一个共享的缓冲区进行数据交换。生产者并不知道消费者如何处理数据，消费者也不知道生产者如何生产数据。

Since the \texttt{WebSocket} module is used in this project, and the \texttt{WebSocket} module itself is implemented based on an asynchronous mechanism, all method calls related are asynchronous functions (async methods). Consequently, modules that contain \texttt{WebSocket} interactions, such as the \texttt{ChargePoint} class, are classified as asynchronous programming modules. Other parts such as data processing, business logic, and control flow still use the synchronous programming mode to maintain the clarity and intuitiveness of traditional synchronous calls. In order to isolate these two programming modes, this project adopts the producer-consumer design pattern and transmits data through signals at the same time. The producer-consumer pattern decouples producers and consumers, allowing them to run independently and exchange data through a shared buffer. Producers do not know how consumers process data, and consumers do not know how producers generate data.

% 本项目中，生产者为同步模块，负责生成OCPP消息以及对数据进行处理；消费者为异步模块，负责对生成的OCPP消息进行发送处理。该模式主要在\texttt{sys\_basis.Port\_OCPP\_WebSocket\_Client.PortOCPPWebsocketClient}中实现。\texttt{PortOCPPWebsocketClient}类作为OCPP消息客户端端口，内部设计了专门的消息队列\texttt{\_\_list\_request\_message}用于存放待发送的OCPP消息。其核心机制如下：

In this project, the producer is a synchronous module responsible for generating \ac{OCPP} messages and processing data, while the consumer is an asynchronous module dedicated to transmitting and handling the generated \ac{OCPP} messages. This pattern is primarily implemented in \texttt{sys\_basis.Port\_OCPP\_WebSocket\_Client.\\PortOCPPWebsocketClient}. The \texttt{PortOCPPWebsocketClient} class serves as the \ac{OCPP} message client port and internally maintains a special message queue,\\\texttt{\_\_list\_request\_message}, to store \ac{OCPP} messages pending transmission. The core mechanism operates as follows:

% 当运行\texttt{start()}时，将启动一个异步协程任务\texttt{\_\_send\_request\_message}。该任务在一个\texttt{while}循环内持续监听消息队列\texttt{\_\_list\_request\_message}。当消息队列为空时，\texttt{while}循环被异步事件\texttt{\_\_event\_request\_message}阻塞，进入等待状态，避免无意义的轮询造成资源浪费。

When \texttt{start()} is executed, it starts an asynchronous coroutine task\\\texttt{\_\_send\_request\_message}. This task continuously listens to the message queue\\\texttt{\_\_list\_request\_message} within a \texttt{while} loop. When the message queue is empty, the \texttt{while} loop is blocked by the asynchronous event \texttt{\_\_event\_request\_message}, entering a waiting state to avoid unnecessary polling and resource waste.

% 而在同步模块中，当需要发送OCPP消息时，会调用同步方法\texttt{send\_request\_message(message)}，该方法会将生成的消息\texttt{message}放入消息队列\texttt{\_\_list\_request\_message}中，同时释放异步事件\texttt{\_\_event\_request\_message}，从而唤醒处于阻塞状态的\texttt{while}循环。异步循环被唤醒后，从消息队列中以此取出消息，并调用异步方法\texttt{self.\_\_charge\_point.send\_request\_message(self.\_\_list\_request\_message.pop(0))}发送消息。当队列为空时，再次设置异步事件\texttt{\_\_event\_request\_message}阻塞\texttt{while}循环。

In the synchronous module, when an \ac{OCPP} message needs to be sent, the synchronous method \texttt{send\_request\_message(message)} is called. This method places the generated messages into the message queue \texttt{\_\_list\_request\_message} and releases the asynchronous event \texttt{\_\_event\_request\_message}, which wakes up the \texttt{while} loop that is in a blocked state. After the asynchronous loop is awakened, it retrieves the messages from the message queue and calls the asynchronous method\\\texttt{self.\_\_charge\_point.send\_request\_message(self.\\\_\_list\_request\_message.pop(0))} to send the messages. When the queue is empty, the asynchronous event \texttt{\_\_event\_request\_message} is set again to block the \texttt{while} loop.

% 这样就通过消息队列\texttt{\_\_list\_request\_message}将同步模块与异步模块进行了隔离。其好处在于:

% \begin{itemize}
%     \item 同步模块专注于数据生成和业务逻辑处理，无需关心异步机制
%     \item 异步模块专注于通信处理，专门负责异步发送消息
%     \item 两者通过消息队列和事件机制进行解耦，避免直接调用导致的异步“污染”
%     \item 当消息队列为空时，异步循环再次被阻塞，直到新的消息到来，从而保证了系统资源的高效利用，减少了等待开销
%     \item 提升了项目代码的可读性、可维护性和可扩展性
% \end{itemize}

Thus, the synchronous module and the asynchronous module are isolated through the message queue \texttt{\_\_list\_request\_message}. The benefits of this approach are as follows:

\begin{itemize}
    \item The synchronous module focuses on data generation and business logic processing, without concerning the asynchronous mechanism. 
    \item The asynchronous module focuses on communication processing, specifically handling the asynchronous sending of messages. 
    \item Both modules are decoupled through the message queue and event mechanism, avoiding the "contamination" caused by direct asynchronous calls. 
    \item When the message queue is empty, the asynchronous loop is blocked again, until a new message arrives, ensuring the efficient use of system resources and reducing waiting cost. 
    \item It improves the readability, maintainability, and scalability of the project code. 
\end{itemize}

% chapter 4
\chapter{CSMS}
\label{chap:CSMS}

% 建议“用电”从“electrical usage” 换成“electrical consumption”
% 在电动汽车充电系统中，CSMS（Charging Station Management System，充电站管理系统）是一个核心软件系统，负责管理和协调多个充电站、充电桩以及用户的操作。它通常运行在云端或本地服务器上，为充电运营商提供监控、控制、计费和维护等功能。

% CSMS 是整个充电基础设施的“大脑”，但在本项目中将CSMS的功能进行了简化，忽略了认证和数据统计功能，重点实现了通信和优化计算的功能。

% CSMS的主体结构分为4个部分：server主函数，ocpp通讯，优化器和网页。ocpp通讯和网页分别在\autoref{chap:SystemBase}和\autoref{chap:Front-end Display}中介绍。

% 本章节主要介绍CSMS中使用的方法类DataGene，优化器类Optimizer和主函数Server。

In an electric vehicle charging system, the \ac{CSMS} is the core software system responsible for managing and coordinating multiple charging stations, charging points, and user operations. It typically runs on cloud servers or local servers, providing charging operators with functionalities such as monitoring, control, billing, and maintenance\cite{CSMS}. 

\ac{CSMS} serves as the "brain" of the entire charging infrastructure. However, in this project, the functionality of \ac{CSMS} has been simplified, omitting authentication and data statistics while focusing on communication and optimization calculations.

The \ac{CSMS} framework is divided into four main components: the main server function, \ac{OCPP} communication, the optimizer, and the web interface. The \ac{OCPP} communication and web interface are introduced in \autoref{chap:SystemBase} and \autoref{chap:Front-end Display}, respectively.

This chapter primarily introduces the key components of \ac{CSMS} used in this project, including the utility class \texttt{DataGene}, the optimizer class \texttt{Optimizer}, and the main server function \texttt{Server}.

% section 5.1
%\section{方法类DataGene}
\section{DataGene utility class}
\label{sec:DataGene}
% 在优化器的设计中，采用了一系列通用的静态方法，这些方法被统一放在了DataGene类中，旨在提高系统的灵活性和可维护性。该类中的方法涵盖了多项功能，主要包括以下六个方面：
In the design of the optimizer, a series of general static methods are used, which are collectively placed in the \texttt{DataGene} class to enhance system flexibility and maintainability. The methods in this class cover multiple functions, mainly including the following six aspects:
\begin{enumerate}
    %\item 时间戳与字符串的转换\\
    %time2str() 和 str2time() 方法实现了datetime格式与字符串的互相转换。考虑到OCPP协议中WebSocket消息的时间戳格式要求为\%Y-\%m-\%dT\%H:\%M:\%SZ，而优化器计算时则需要时间戳（ datetime 格式），因此这些方法能有效地将字符串时间转换为时间戳，并兼顾时区和夏冬令时的影响。为此，采用了pytz库来处理时区和夏令时问题，配合datetime库的strftime和strptime函数进行时间格式转换。

    \item Conversion between Timestamps and Strings\\
    The \texttt{time2str()} and \texttt{str2time()} methods implement mutual conversion between the \texttt{datetime} format and strings. Considering that the \ac{OCPP} protocol requires WebSocket message timestamps in the format \texttt{\%Y-\%m-\%dT\%H:\%M:\%SZ}, while the optimizer needs timestamps in \texttt{datetime} format for calculations, these methods effectively convert string-based time representations into timestamps, taking account of the influence of time zones and summer/winter time issues. To achieve this, the \texttt{pytz} library is used to handle time zones and summer/winter time issues, in combination with the \texttt{strftime} and \texttt{strptime} functions from the \texttt{datetime} library for time format conversion.

    % \item 字典键名的格式转换\\
    % snake\_to\_camel\_case() 和 convert\_dict\_keys() 方法解决了字典键命名的不统一问题，特别是在OCPP库中常见的蛇形命名法与驼峰命名法的混用问题。通过这两个方法，可以将字典中的键名统一为优化器所需的格式，增强了代码的可读性与一致性。

    \item Format Conversion of Dictionary Keys\\
    The \texttt{snake\_to\_camel\_case()} and \texttt{convert\_dict\_keys()} methods address inconsistencies in dictionary key naming, particularly the mixed usage of snake case and camel case commonly found in the \ac{OCPP} library. These methods standardize dictionary key names to the format required by the optimizer, improving code readability and consistency.

    % \item 生成电价数组\\
    % gene\_eprices() 方法用于生成符合优化器要求格式的电价数组，确保优化过程中的电费计算准确。这一方法根据白天电价、夜间电价以及相关切换时间，生成一个包括96个15分钟间隔的电价列表。对于没有提供夜间电价或切换时间的情况，系统会默认采用统一电价，以便适应不同的电价策略。

    \item Generate Electricity Price Array\\
    The \texttt{gene\_eprices()} method is used to generate an electricity price array in the format required by the optimizer, ensuring accurate cost calculations during the optimization process. This method generates a list of 96 15-minute intervals, based on daytime and nighttime electricity prices and the corresponding switching times. In cases where nighttime prices or switching times are not provided, the system defaults to a unified price to accommodate different pricing strategies.

    % \item 分割时间段\\
    % split\_time() 方法主要用于将一天或一段时间的用电记录、电价以及电网功率按照指定时间段进行切割，形成数组形式，以便优化器在时间段层面进行优化。这一功能尤其在需要考虑不同时间段电力需求变化时显得尤为重要。

    \item Split Time Period\\
    The \texttt{split\_time()} method is primarily used to split electricity usage records, electricity prices, and grid power over a specified time period into segments, forming an array for the optimizer to perform optimization at the time period level. This functionality is particularly important when considering the variation in power demand across different time periods.

    % \item 生成用户的用电功率历史记录\\
    % gene\_his\_usage() 方法使用np.random.normal()生成随机的家庭用电功率历史记录，模拟家庭在不同时间段的电力需求波动。该方法特别设计了白天和晚上的用电高峰期，并且支持通过固定种子来生成固定的历史用电记录，便于不同优化模式的比较和实验。

    \item Generate User's Power Usage History\\
    The \texttt{gene\_his\_usage()} method uses \texttt{np.random.normal()} to generate random historical power usage records for a household, simulating fluctuations in electricity demand at different times of the day. The method is specifically designed with peak usage periods for day and night, and it also supports generating fixed historical usage records by setting a fixed seed, facilitating comparisons and experiments with different optimization modes.

    % \item 充电图像的绘制\\
    % plot\_usage()、plot\_charging\_curve()、plot\_usage\_comparison() 和 plan2figure() 四个方法用于不同的充电数据可视化。plot\_usage()展示了历史用电折线图；plot\_charging\_curve()展示了电车已充电量随时间的变化曲线；plot\_usage\_comparison()用于对比优化前后的用电功率与电网最大功率，更加直观显示优化效果；plan2figure()则提供了充电过程的实时更新，显示当前和预计的充电量。

    \item Drawing Charging Graphs\\
    The methods \texttt{plot\_usage()},\texttt{plot\_charging\_curve()},\\\texttt{plot\_usage\_comparison()} and \texttt{plan2figure()} are used for visualizing different charging data. \texttt{plot\_usage()} displays the historical electricity usage line graph; \texttt{plot\_charging\_curve()} shows the power variation curve during the electric vehicle charging process; \texttt{plot\_usage\_comparison()} compares the household's power usage before and after optimization with the maximum grid power, visually showing the optimization effect; \texttt{plan2figure()} provides real-time updates of the charging process, displaying the current and estimated charging amounts.

\end{enumerate}
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

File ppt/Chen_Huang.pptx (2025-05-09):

## ADP - Charging Station Upgrade to OCPP Communication for Smart Charging

- reported by Junfan Jin, Can Zeng, Yunan Jiang and Huang Chen

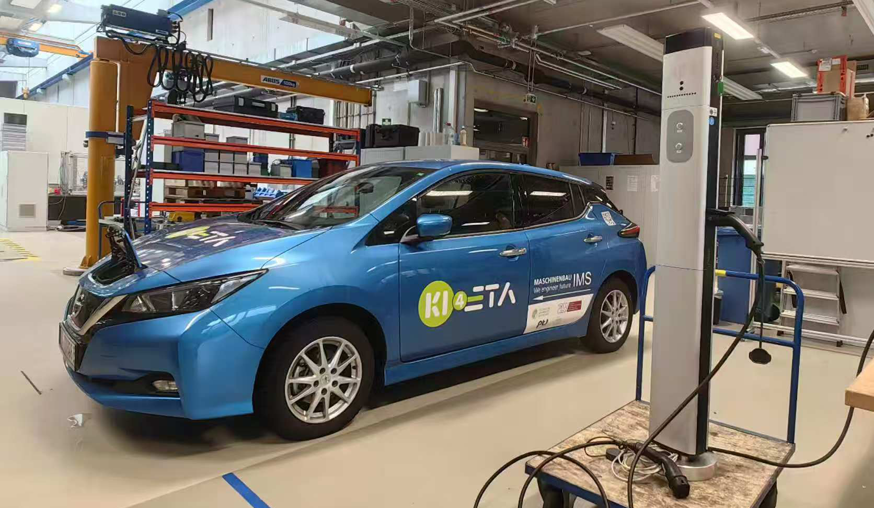
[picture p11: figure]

## Background

1, Increasing number of
EVs & Charging Stations
2, In Germany, “plug and
charge” mode of 10 million
EVs by 2035 increase 50%
in low-voltage grid and
transformer costs [1]


Figure 1: Charge station sales increasing over the years [2]

## Significance

OCPP

- Open source

Peak shaving

- Decrease overload of grid

Variable charging rate

- Electricity price
- Battery capacity
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

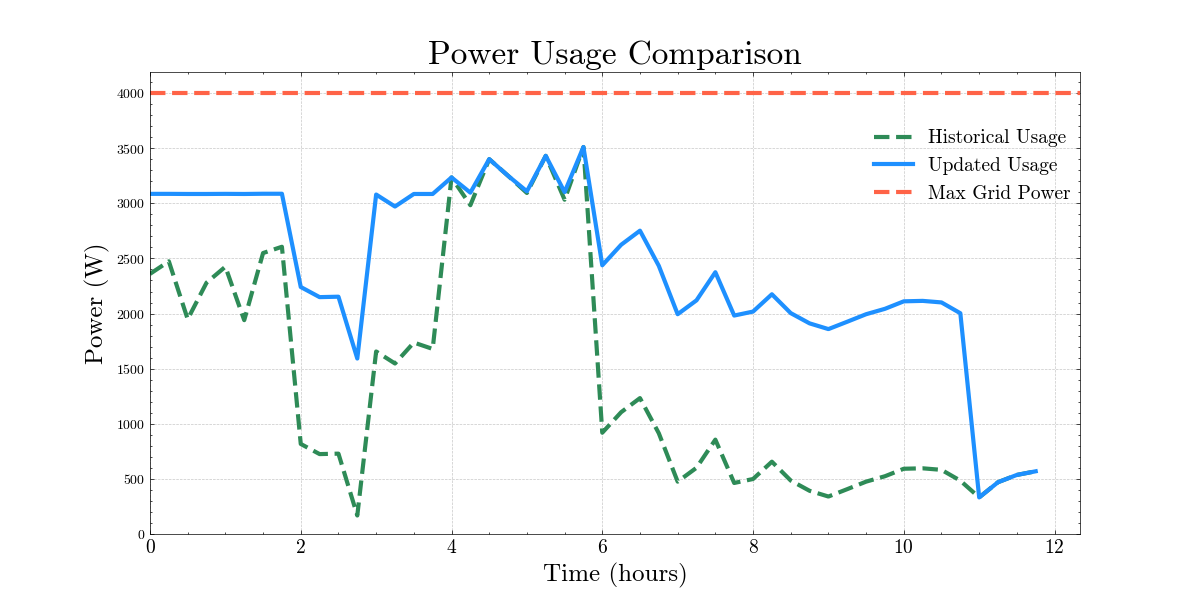
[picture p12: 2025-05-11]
paper/img/mod_0.png

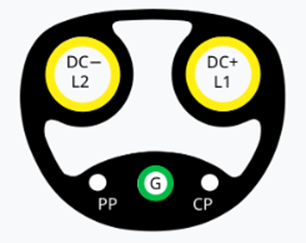
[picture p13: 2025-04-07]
paper/img/SAEJ3400.jpg

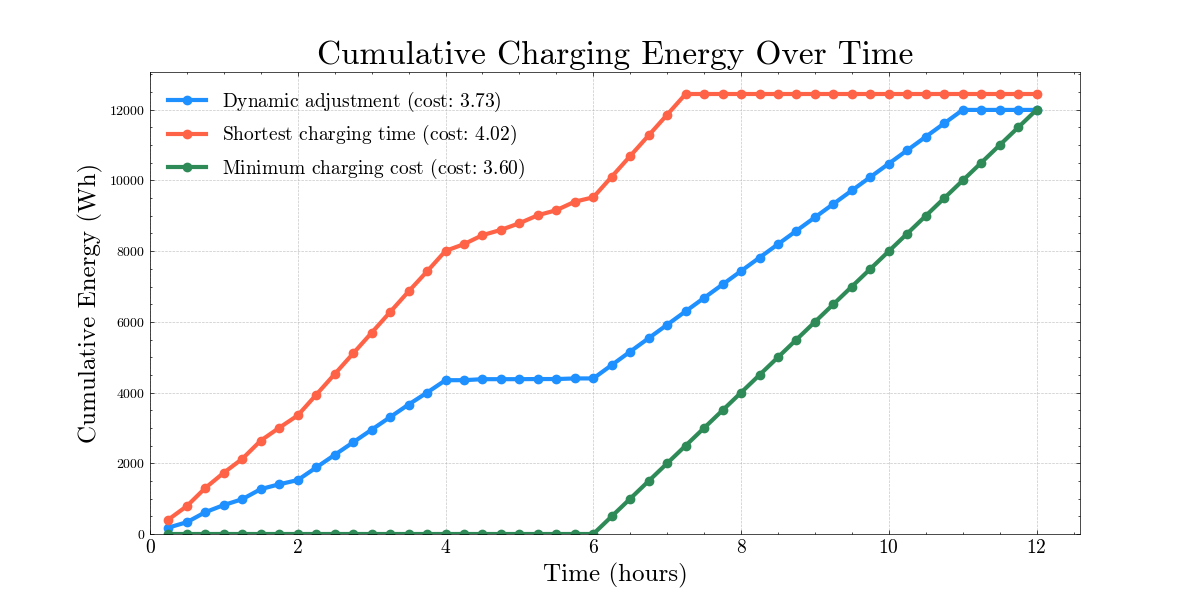
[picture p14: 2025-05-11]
paper/img/modcomparison.png

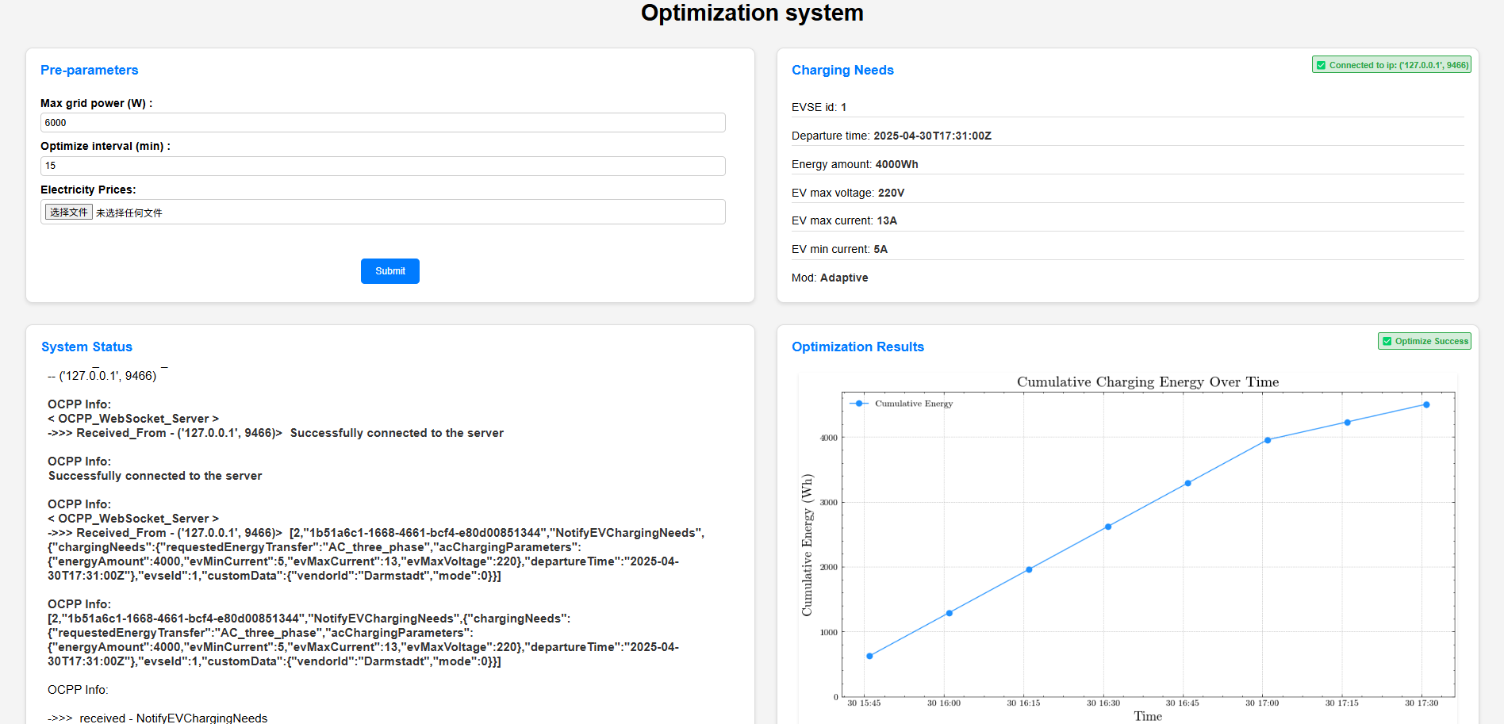
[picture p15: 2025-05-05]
paper/img/web_opt.png

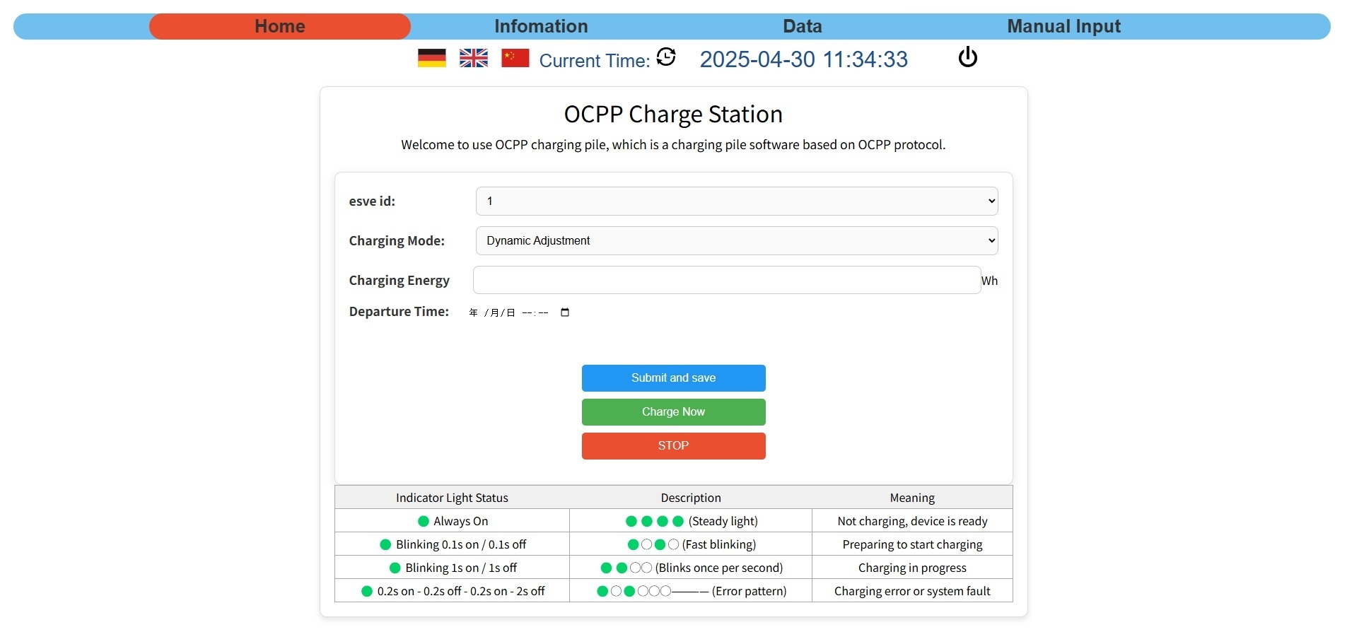
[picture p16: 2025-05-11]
paper/img/light_GUI.png

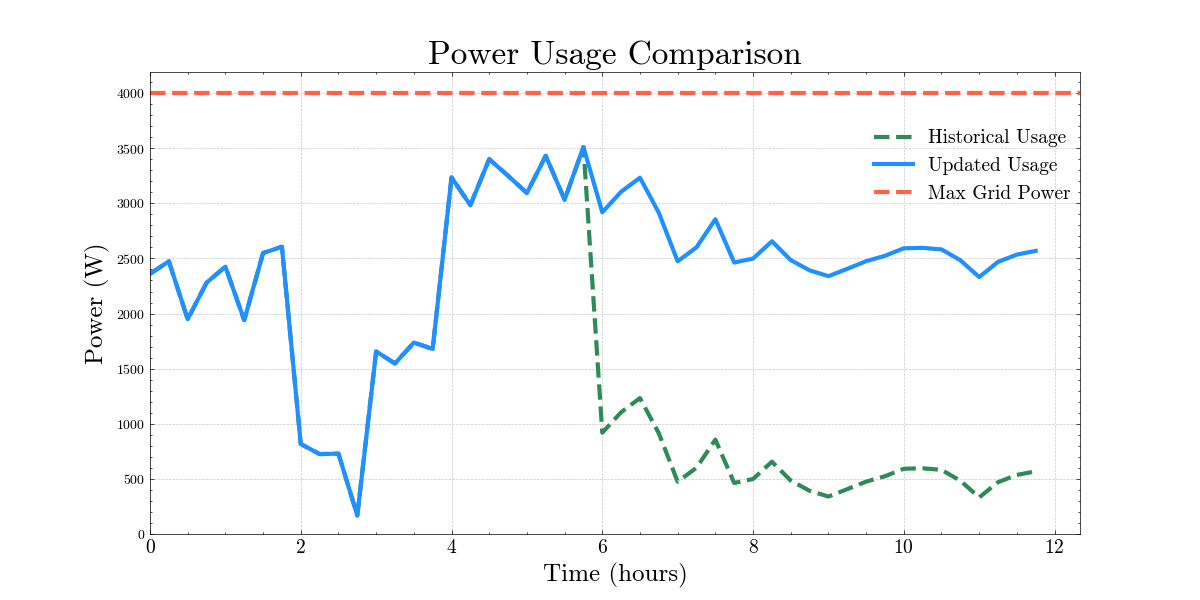
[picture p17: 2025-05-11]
paper/img/mod_2.png

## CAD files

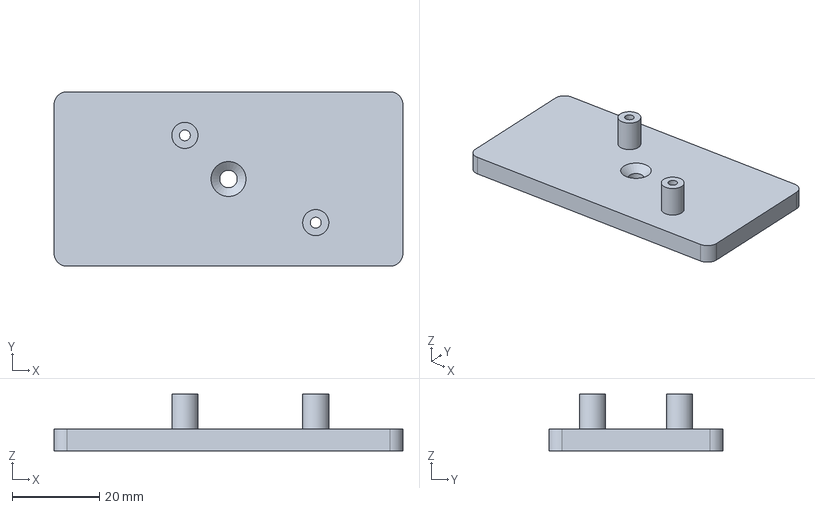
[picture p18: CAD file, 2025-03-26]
dev/3DModel/FreeCAD/HV_Teil.FCStd
80.0 x 40.0 x 13.0 mm

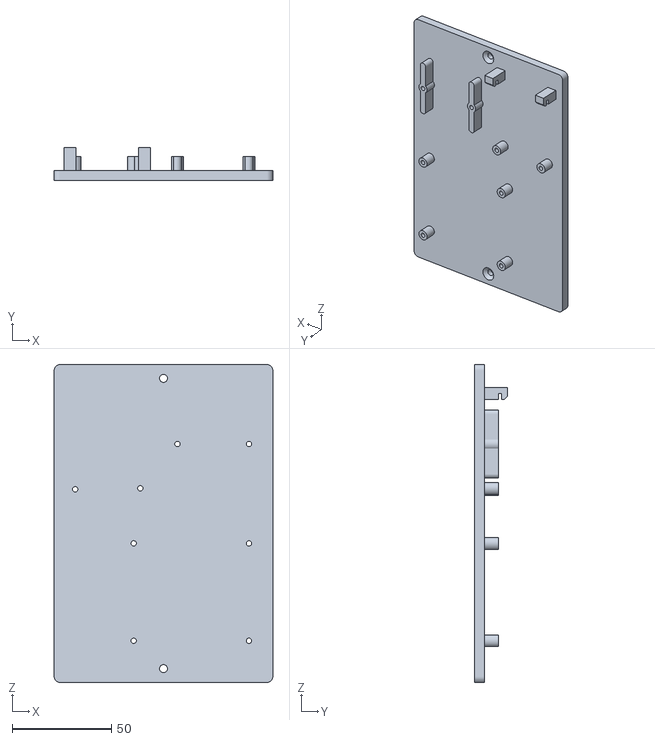
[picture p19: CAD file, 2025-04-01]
dev/3DModel/SolidWorks/LV.STL
110.0 x 16.7 x 160.0

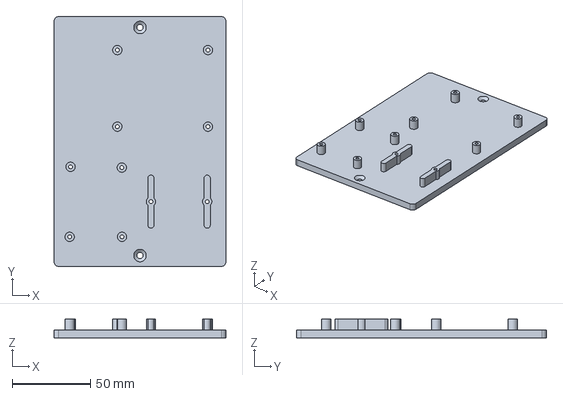
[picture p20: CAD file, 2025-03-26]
dev/3DModel/FreeCAD/LV_Teil.FCStd
110.0 x 160.0 x 12.0 mm

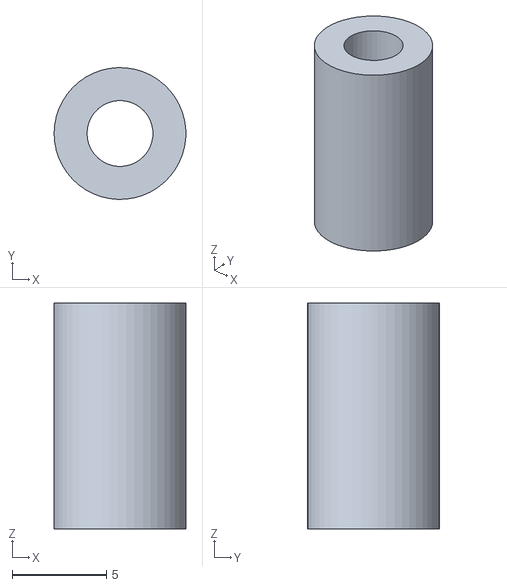
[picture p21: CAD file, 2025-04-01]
dev/3DModel/SolidWorks/Rohr.STL
7.00 x 7.00 x 12.0

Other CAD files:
dev/3DModel/FreeCAD/HV_Teil.stl
dev/3DModel/FreeCAD/LV_Teil.stl

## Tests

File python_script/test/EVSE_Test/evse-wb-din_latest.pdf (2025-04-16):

# EVSE

## Wallbox, DIN, W16

## datasheet

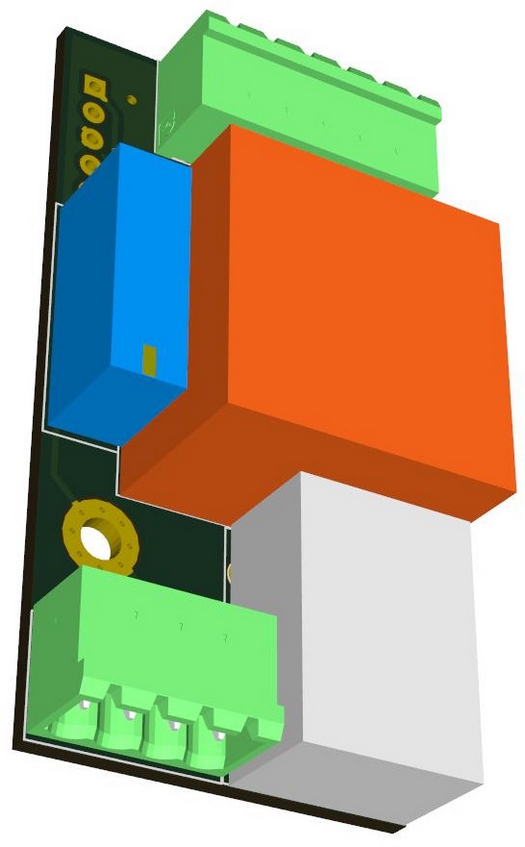
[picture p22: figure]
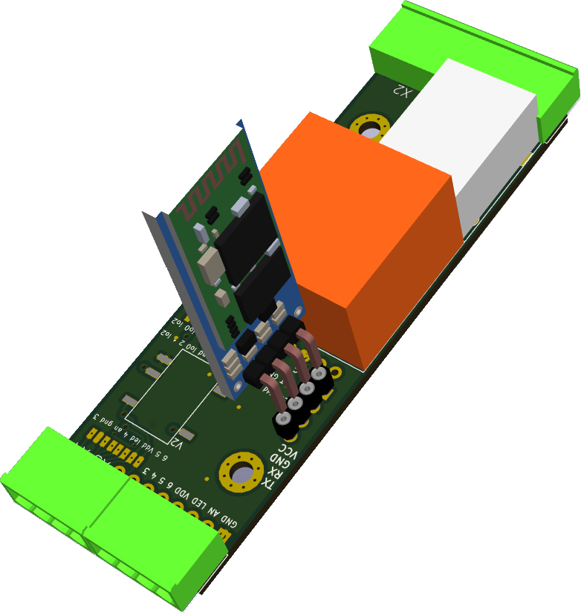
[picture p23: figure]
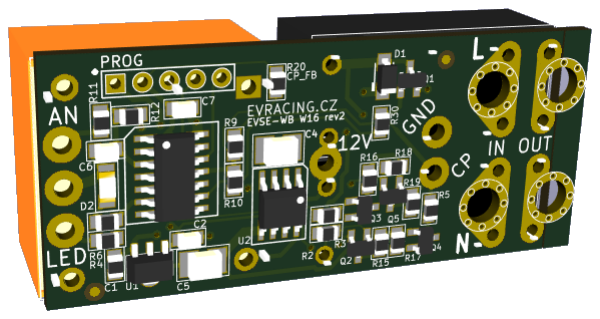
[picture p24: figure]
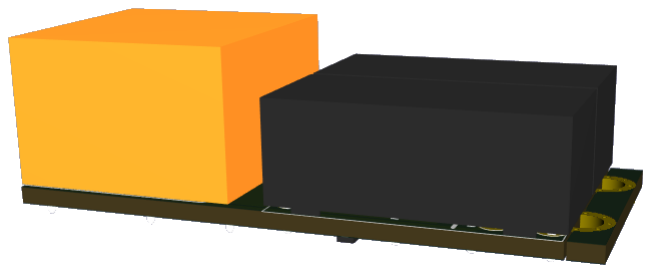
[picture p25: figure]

*) these are 3D generated models, real product can look differently and have different accessories

Last document update: August 31, 2021

## Table of Contents

## Introduction

EVSE stands for electric vehicle supply equipment. It is an element that supplies electric energy for the recharging of electric or plug-in vehicles.
Read me first
The EVSE board is supplied with default 32A settings (or 16A for EVSE W16). Please check the chapter “Customizations” for more information about further possibilities of changing maximum charging current. 220 Ohm RPP is included with the kit (EVSE WB). Theory of operation
Pilot signal duty cycle provided by EVSE defines maximum charging capacity. The car can define several states by pulling the pilot signal down to certain voltage levels (3V, 6V, 9V). Based on this feedback EVSE will trigger the relay for the vehicle to charge or evaluate the state as an error (electricity will not be provided to the output socket/connector).
For more information please check:
- http://en.wikipedia.org/wiki/IEC_62196
- http://en.wikipedia.org/wiki/SAE_J1772
- https://github.com/kortas87/simple-evse/wiki (https://code.google.com/p/simple-evse/)

### Resistance PP-PE (max cable throughput)

Resistance [ohm] | Current limit [A] | Wire cross-section [mm² ]
> 1500 * | 6 | --
1500 | 13 | 1.5
680 | 20 | 2.5
220 | 32 | 6
100 | 63 | 16
<100 ** | 80 | –
* | no resistor connected
** recommended ~50 Ohm

Compatibility
- Tesla Model S
- Nissan Leaf
- Mitsubishi iMiev (Peugeon iOn, Citroen cZero)
- Opel Ampera
- eGolf
- Mitsubishi Outlander PHEV
- Citroen Berlingo Electrique
- and others...

## General description EVSE WB, DIN, W16

### Parameters

Supply voltage | 90 – 265 VAC
Power consumption | <1W
AC/DC power | 1W or 3W
Operating temperature | -20 to 80 °C
Protection index | IP00
Onboard resistor for external LED | 1k
Vehicle compatibility | all vehicles according to IEC 62196
Connection options | HC06 bluetooth, UART-USB converter, wifi ESP8266, ethernet USR-TCP232/GSM, ...

All boards are based on the same software and hardware. Main differences between each other are described in this table:

EVSE | WB | DIN | W16 | W50
DIN rail mounting | yes with 3D printed case *) | yes | no | yes
PP detection | yes | yes | no | yes
power relay | no | no | yes 2x16A **) | yes 4x50A
3phase | yes | yes | no **) | yes
fits inside Type2 or Type1 | no | no | yes | no
wiring | easy | easy | medium | easy
supports vehicles | all | all | all | all
uart communication | yes | yes | yes | yes
in production | yes | yes | yes | late 2019
*) 3D data available on request
**) possible to change for 1x32A Panasonic relay with the same size or add another 2pcs 16A relay to get compact 11kW 3phase charger (wiring = difficult)

## EVSE WB - board description

### Parameters

Dimension (without connectors) | 60 x 30 x 25 mm
Mounting holes spacing | 30 x 20 mm
Relay | 5A 250V
Weight | 80 g
Order code | EVSE-WB
Options | HC06 bluetooth, UART-USB converter

EVSE WB board has 2 connectors. 4-pin X1 for high voltage side and 6-pin for signaling wires and control purposes. There is also PROG connector used for flashing new firmware (ICSP), additional communication and can be further used for adjusting EVSE current (see “Customizations” chapter).

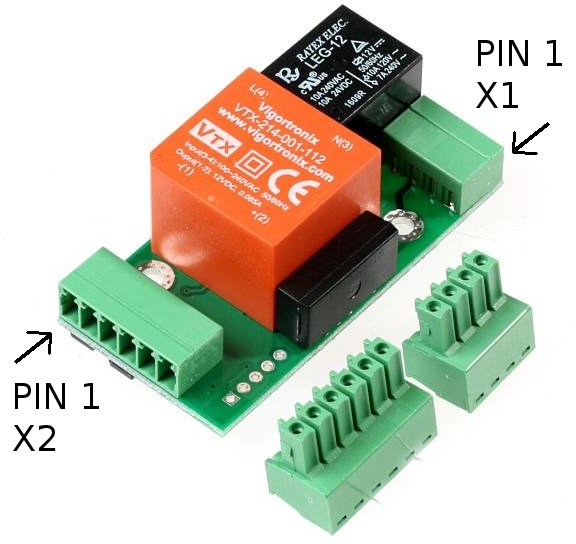
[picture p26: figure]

Picture 1: EVSE WB

### X1 connector = 4pins

pin | name | description
1: L | phase | 230V power supply for EVSE board and external
| neutral | contactor 2: N
3: PE | protection-earth | Ground reference
4: rel | relay output | This output drives coil of an external contactor Maximum allowed current is 3A.

### X2 connector = 6pins

pin | name | description
1: CP | control pilot | To vehicle connector
2: PP | proximity pilot | To vehicle connector
3: 5V | 5V power output | Used as a power supply for external components (max 40mA)
4: GND | ground | Ground reference
5: LED | external LED | Includes 1k resistor onboard, connects to LED anode against ground
6: AN | analog input | Used for button or current sensor input

### PROG connector = 5pin header

pin | name | description
1 | VPP | ICSP** / RFU* [marked by rectangle] from Jan 2018 bootloader enable pin
2 | VDD | 5 V
3 | GND | Ground
4 | DAT / TX | ICSP** / current boost / communication function
5 | CLK / RX | ICSP** / current limit / communication function
* reserved for future use
** firmware upgrade interface

## EVSE DIN - board description

(for reference only, was replaced by EVSE-DIN v2 during 2020, see details below)

### Parameters

Dimension (without connectors) | 86 x 29 x 25 mm
Mounting holes spacing | 54 x 18 mm
Relay | 5A 250V
Weight | 85 g
Order code | EVSE-DIN
Options | RS485 driver, HC06 bluetooth, UART converter, 3W AC/DC

For the minimum installation you can only wire 6pin X1 connector (required: L,N,REL,PE,PP,CP).

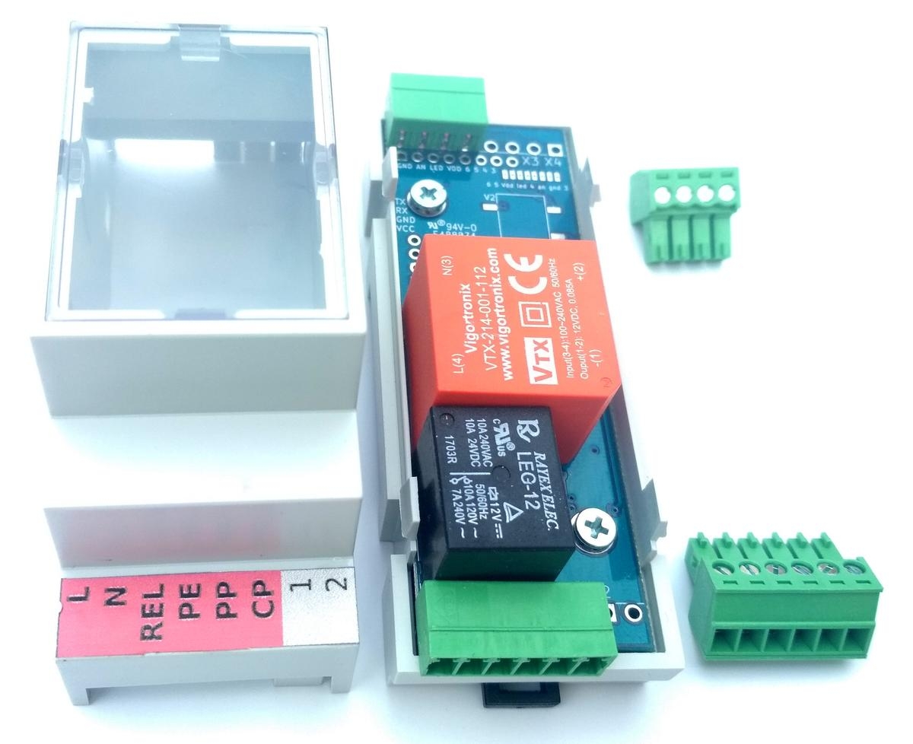
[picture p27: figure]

Picture 2: EVSE DIN

### X1 connector = 6pins

pin | name | description
1: L | phase | 230V power supply for EVSE board and external
| neutral | contactor 2: N
3: rel | relay output | This output drives coil of an external contactor Maximum allowed current is 3A
4: PE | protection-earth | Ground reference
5: PP | proximity pilot | To vehicle connector
6: CP | control pilot | To vehicle connector

### X2 connector = 2pins (OPTION)

pin | name | description
1:1 | | function defined by extension module
2:2 | | function defined by extension module

### X3 connector = 4pins

pin | name | description
1: 5V | 5V power output | Used as a power supply for external components (max 40mA)
2: LED | external LED | Includes 1k resistor onboard, connects to LED anode against ground
3: AN | analog input | Used for button or current sensor input
4: GND | ground | Ground reference

### X4 connector = 4pins (OPTION)

pin | name | description
1:3 | | function defined by extension module
2:4 | | function defined by extension module
3:5 | | function defined by extension module
4:6 | | function defined by extension module

### PROG connector = 5pin header (OPTION)

same function as EVSE WB

### UART connector = 4pin header (OPTION)

can be used for direct connection of HC06 (female header)

## EVSE DIN v2 - board description

Version 2020

### Parameters

Dimension (without connectors) | 86 x 29 x 25 mm
Fusing | Integrated fuse
Relay | 5A 250V
Weight | 85 g
Order code | EVSE-DIN
Terminals | Push terminals
Options | RS485 module, HC06 bluetooth, UART converter, locking module

For the minimum installation you can only wire 4pin X1 connector (required: L,N,REL,PE) + X2 (required CP)

Picture 3: EVSE DIN v2

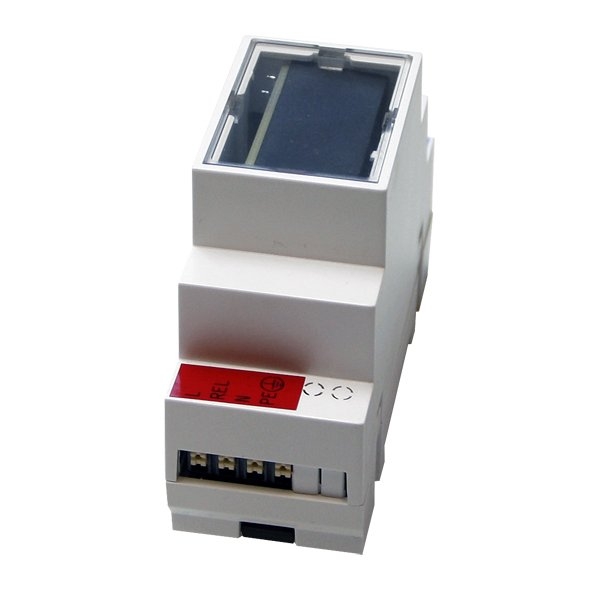
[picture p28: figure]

### X1 connector = 4pins (push terminals)

pin | name | description
1: L | phase | 230V power supply for EVSE board and external contactor
2: REL | relay output | This output drives coil of an external contactor maximum allowed current is <1A, fused
3: rel | neutral | 230V power supply for EVSE board and external contactor
4: PE | protection-earth | Ground reference

### X2 connector = 8pins (push terminals)

pin | name | description
1:CP | control pilot | To vehicle connector
2:PP | proximity pilot | To vehicle connector
3:12V | Power output | Possible to power external components. Default 12V, can be switched to 5V by onboard resistor jumper X7 (max 100mA)
4:GND | Ground reference | PE
5:LED | external LED | Includes 1k resistor onboard, connects to LED anode against ground
6:AN | analog input | Used for button or current sensor input
7:A | | function defined by extension module
8:B | | function defined by extension module

### PROG connector = 5pin header

same function as EVSE WB, part of the X3 header

### UART connector = 4pin header

can be used for direct connection of HC06 (female header), part of the X3 header

## EVSE W16 - board description

### Parameters

Dimension rev2 | 59 (55) x 26 x 22 mm
Dimension rev3 | 58 x 25 x 20 mm
Relay (default) | 2x16A 250V
Relay option 32A | 1x32A
Weight | Approx. 50 g
Order code | EVSE-W16 (2x16A relay) EVSE-W16_32A (1x32A relay)
Options | HC06 bluetooth, USB-UART converter

EVSE-W16 is the smallest board and also includes power relays for 16A. It can be considered as a successor of the original Simple EVSE, but with improved CP driver to support all vehicles, new software and AC/DC + relay integration. Solderable terminals instead of plugs keep it smaller. It can be mounted in many kinds of small boxes including Type1 or Type2 female connectors.
EVSE-W16 rev3 (May 2020) is upgraded version with following advantages:
- better surge rating and optimized component layout
- integrated fuse and inrush current limiter
- option for 32A relay (one phase type1/type2 ~7kW charger)

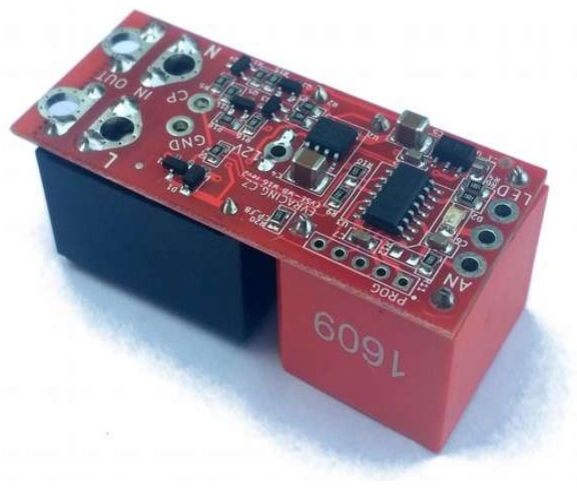
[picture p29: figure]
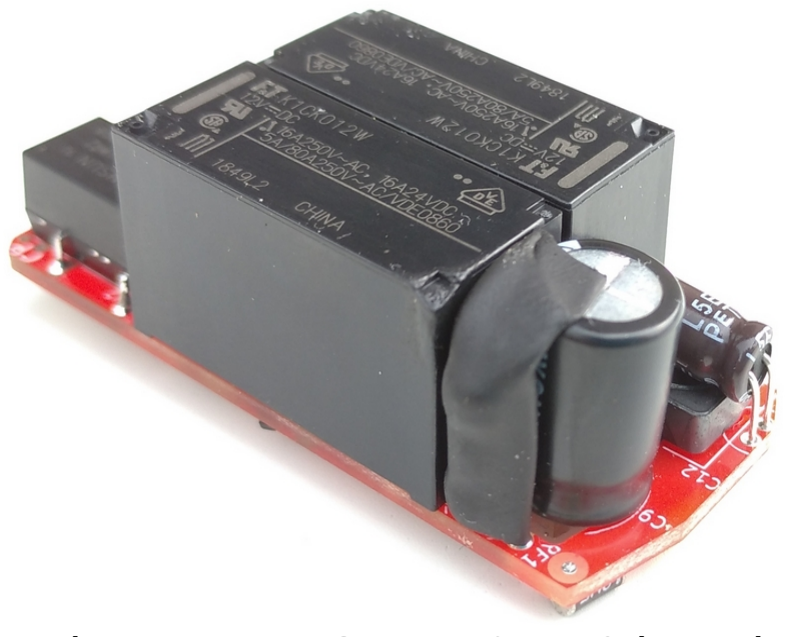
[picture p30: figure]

Picture 4: EVSE W16 rev2 board | Picture 5: EVSE W16 rev3 board

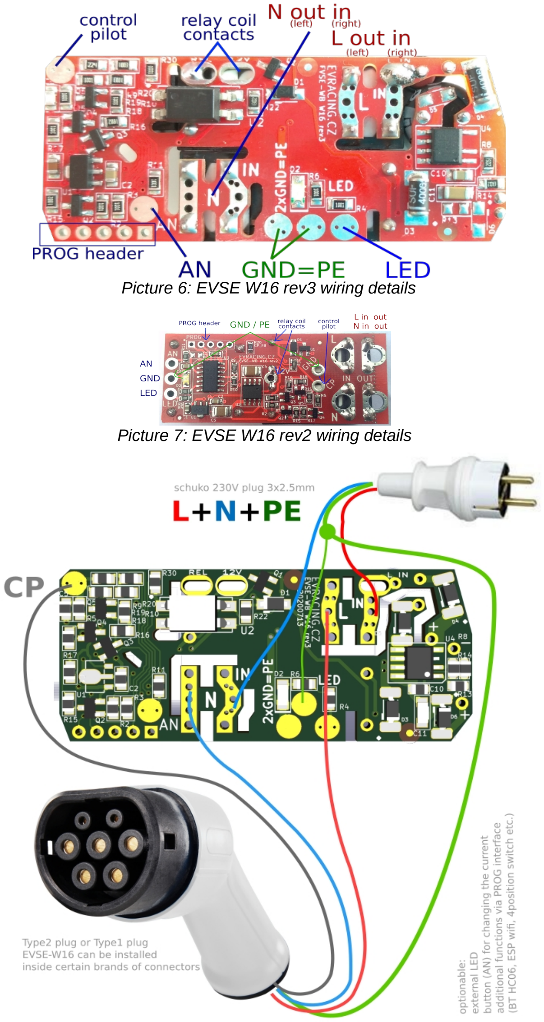
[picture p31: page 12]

Picture 6: EVSE W16 rev3 wiring details

Picture 7: EVSE W16 rev2 wiring details

### pins overview

pin | name | description
L in | phase | 230V power supply for EVSE board + power input
N in | neutral
L out | phase | switched power output for the EV connector
N out | neutral
PE | protection-earth | = GND
CP | control pilot | To vehicle connector (Type1 or Type2)
LED | external LED | Includes 1k resistor onboard, connects to LED anode against ground
AN | analog input | Used for button or current sensor input
GND | ground | Ground reference (+ second GND between AN and LED), this is also PE reference
12V, - | relay coil contacts | can be used for adding relays for 3phase charger

### PROG connector = 5pin header (OPTION)

same function as EVSE WB

## Customizations

Current limitation A – using PROG pin 5
Check the table for details of how you can set the maximum current. This settings will override PIN 4 settings.
PROG connector | connection | current limit | register
pin5 > 4.5 V | open (internal pull-up only) | 32 A [default] | 2000
2.5 V < pin5 < 4.5 V | 100-200k* resistor to GND | 25 A | 2013
0.2 V < pin5 < 2.5 V | ~3-20k* resistor to GND | 16 A | 2012
pin5 < 0.2 V | tied to GND | 10 A | 2011
* resistor value may differ since internal pull-up has no defined value from production (~50k supposed), in most cases 100k for 25A and 5k for 16A is recommended


Current limitation B – using PROG pin 4
Check the table for details of how you can set the maximum current.
PROG connector | connection | current limit | register
pin4 > 4.5 V | open (internal pull-up only) | 32 A [default] | 2000
2.5 V < pin4 < 4.5 V | 100-200k* resistor to GND | 48 A | 2015
0.2 V < pin4 < 2.5 V | ~3-20k* resistor to GND | 63 A | 2016
pin4 < 0.2 V | tied to GND | 80 A | 2017
* resistor value may differ since internal pull-up has no defined value from production (~50k supposed), in most cases 5k for 63A and 100k for 48A is recommended

Picture 8: PROG header location on EVSE-WB board

Precise current setting with Analog Input
Press and hold button connected to Analog input AN of for a few seconds until LED starts to blink rapidly. Then count LED blinks which correspond to number of ampers. Please note that this limit will be set until you reboot the EVSE (make a power cycle). Button is connected the way that it pulls the signal down to ground (level <1V).

Current limitation based on PV production
We recommend to use any kind of control system (smart home PLC, Beaglebone with RS485 and SDM630 electricity meter, SDS micro...) and control the EVSE current continuously either by voltage input AN, via data communication (UART/RS485), or simply in 2 or more steps by relay outputs (EVSE is off, EVSE current low, EVSE current high). Each system is different as well as customer needs.

## Application examples


In these application examples we suppose that customer uses appropriate contactor with 230V coil. Please check section “Recommended contactors”.

3phase wallbox with keyswitch and low tarif signal input
Keyswitch can be used to lock (disable) / unlock (enable) wallbox (access control).

4position rotary switch details Values 10/16/25/32 [A] can be customized.

_

3phase wallbox including a cable and plug
In this example we make 3 phase Wallbox using DSIEC-2E cable. PWM duty will be limited by the size of RPP (refer to the Theory of operation chapter). If you do not connect any RPP current will be limited to only 6A. If your EVSE includes a cable which is fixed then you can hard-wire RPP resistor for cable's nominal value.


Picture 9: EVSE WB type2 fixed cable

32A EVSE with connector J1772
With EVSE Wallbox board you can quickly build a charging station for your Nissan Leaf 6.6kW or any other vehicle equipped with J1772 plug.

Optional Analog Input connection:
The internal J1772 connection allows to use S1 proximity button as an auxiliary button for EVSE. With the help of this button you can easily change charging current with the smallest step of 1A (see Features -Precise current setting).


Picture 10: J1772 proximity button connection detail


Picture 11: J1772 connector - signal and power wires

Recommended contactors
You should use relays / contactors equipped with 230V coil and connect them directly to the board connector X1. Here are some examples which relays can be used. The most common one (4pole contactor 25A) can be easily obtained in local electrical accessories shop (Conrad, K&V Elektro...)
- 3-phase, maximum current 20A (e.g. Tesla 11 kW):
Noark Ex9CH25 40, Elko VS420
- 3-phase, maximum current 40A (e.g. Tesla 16.5 / 22 kW, ZOE 22 kW): Elko VS440, Eaton Z-SCH 230V/25-40
- 1-phase, maximum current 16-20A (e.g. Peugeot iOn 3 kW, Tesla 3-4kW): Eaton Z-R230/S
- 1-phase, maximum current 40A (e.g. Nissan Leaf 6.6 kW):
RELPOL R40N
or use normal 4-pole contactor


Using external 12V relay


In some cases it would be possible to use another 12V coil relay (maximum 0.8W coil consumption), however this approach requires desoldering of the original relay and is recommended only to advanced users. Automotive relays can handle sufficient currents however their voltage rating is not high enough.
Pins marked by pink are connected to a 12V relay coil:

Picture 13: 40A 1phase relay

Picture 12: 20A 3phase relay


Continuous EVSE current regulation using a pot (e.g. 6-32A)
Use AN as EVSE voltage input and connect a potentiometer wiper. The other two terminals are to be connected to GND and 5V. Minimum 6A and maximum 32A can be adjusted in registers as needed.


- set 2003 = 0 analog input current regulation
- set 2000 = 32A maximum current (AN = 5V)
- set 2002 = 6A minimum current (AN = 0V)
See the register table for more details. If you do not know how to change register values, please check “Advanced configuration” chapter.

0 - 10V configuration
Add a 1k resistor R12. R11 is also 1k and it will create a divider 1:1. Please note that this setup is recommended to use only with I/O modules having 0-10V analog output galvanically isolated.

Picture 14: EVSE WB - connecting 12V relay directly

Cable selection guide
rubber cables suitable for electric vehicles (type H07RN-F 450/750V)
type | diameter [mm] | current [A] | weight [kg/m] | application
5G6 + 0,75 | 18-22 | 38 | 0.7 | Type2 female 3phase charger, Type2
| 16-20 | 30 | 0.5 | male to Type2 female extension cable 5G4 + 0.75
5G2.5 + 0.75 | 13-17 | 20 | 0.4
4G6 | 16-20 | 37 | 0.6 | Type1 1phase charger, Type2 male to Type1 extension cable
3G6 | 14-18 | 40 | 0.4 | Type1 or Type2 1phase charger with EVSE built into the connector *)

*) other variants: 3x2.5mm 1phase, 5x2.5mm 3phase


Picture 15: 3G6, 4G6, 5G2.5+0.75, 5G4+0.75, 5G6+0.75


Customer solutions and projects

Picture 17: EVSE WB
in custom box with
4position current
switch

Picture 18: Charging cable made with EVSE DIN together with 4pole contactor in a box

Picture 16: 3D printer box for EVSE WB in comparison to EVSE DIN

Picture 20: Wifi interface for EVSE WB (https://github.com/CurtRod/SimpleEVSE-WiFi)

Picture 19: SDM630 electric meter + EVSE DIN RS485, web interface (http://openwb.de)

## FAQ

1) How many PP resistors do I need?
As described in more detail above in the schematic (page 17), there must be one resistor in Type2 female (car side) and other resistor connected to an EVSE. Both are usually part of the extension cable Typ2 female (car side) to Type2 male (EVSE side). When using a fixed cable (not possible to disconnect from the EVSE) then the size of EVSE PP resistor can be “hardcoded” (modbus versions only, see register 2007 below) or a resistor of a fixed size have to be connected (usually 220 ohm for 32A cable).
2) EVSE does not work (config problem)
Make sure that the EVSE is not turned off (2005 configuration register). If the board does not respond at all, make sure the the UART parameters are correct (9600 baudrate, RX/TX+GND wired correctly). Did not the Modbus address change by accident (reg. 2001)?
Any kind of software / firmware / settings problem can be solved using a PicKIT and reprogramming the board from scratch using MPLAB IPE (do not forget to erase the chip too!). PicKIT 4 can be bought on Farnell (https://uk.farnell.com/search?st=pickit%204). EVSE firmware is ready for download from this link: http://evracing.cz/evse/evse-wallbox/fw_pickit/ .
Parameters and options:
- chip name is PIC16F1825
- “power target circuit from tool” (use 2-2.5V)
- “use high voltage program mode entry”
- pin1 (Vpp) is always marked (both on Pickit and the board too)
- if “power target circuit from tool” does not work, power the board externally
- when everything is ready, select HEX file “Browse” and click “Program”
- after successful programming you will see “Programming complete” in log window
3) LED indication explained
Using the pin LED you can directly connect LED to indicate EVSE status. The output includes 1k resistor. External LED has the same indication function as on-board LED.

LED | State description
| Normal operation:
1x fast + pause | pilot signal is steady +12V, no vehicle connected (can be customized – always ON)
2x fast + pause | PWM signal is generated, vehicle is present
1x long + pause | vehicle requested power, contactor is ON
20x fast in 0.5s | enter or leave current setting mode
1x each 0.3s | current setting mode – one more amper set
| Error states (no charging):
3x fast + pause | EVSE is disabled in software (FW >= 6)
4x fast + pause | Charging with ventilation is disabled (FW >= 13)
5x fast + pause | Pilot signal check failed (FW >= 11)
6x fast + pause | Residual current check failure (FW >= 16)
5) How can I change LED blinking behavior? Can I have more LEDs?

Default blinking can be changed by changing board configuration. For example: option 1:
- change bit2 in register 2005 to gain constant LED ON while no EV is connected option 2:
- change bit8 in register 2005 to get separate LED for error signaling (connected to AN) and disable AN pullup bit6
5) How to keep current settings after grid failure?
- see “advanced configuration” and enable communication (if necessary), see NOTE#1
- see HC06 bluetooth module + Android app
- set 2004 = 1 to save current set by button OR
- set 2000 = “desired amp value” to keep this maximum current every time
6) Communication does not work?
- check wiring GND, RX (goes to TX), TX (goes to RX) of your USB-UART converter
- check wiring A+ B- of your USB-RS485 converter (for RS485 variants only)
- to avoid software and configuration problems please use these scripts for testing: https://github.com/kortas87/evse-scripts
- do not forget to enable communication (see NOTE#1)

## Advanced configuration

Beginning January 2018 all boards can be configured by MODBUS. By default MODBUS interface is disabled and old functions of PROG pins are kept. However you can enable it by grounding PIN4 and PIN5 of PROG connector while powering the board up please see NOTE#1 instead.
Physical layer is not galvanically isolated UART (0-5V) or optionable isolated RS485 EVSE DIN only.
The default device ID is 1 (can be changed in register 2001).
Some values can be then read or written over MODBUS protocol. PROG pin header is used for this purpose with following pinout:
PROG connector | connection
pin3 | GND
pin4 | TX
pin5 | RX

This feature is useful for further development and testing with EVSE Wallbox board and can be also a great way to interface other devices such as Raspberry PI, Ethernet UART bridges (e.g. WIZnet or USR serial-to-ethernet boards), various WiFi modules etc.

HC06 bluetooth module + Android app
Preferred way is to use HC06 Bluetooth converter and Android application developed for this purpose. By default the communication is disabled (see NOTE#1 below register table), because the original analog functions of RX,TX pins are kept (for changing current by resistors).
You can download and install the app from here (*.apk extension): http://evracing.cz/evse/evse-wallbox/
HC06 is connected to PROG connector.
1. power up the board, HC06 should start blinking
2. pair your Android device with the adapter (default pin 1234)
3. open the EVSE app and choose the paired bluetooth adapter in its settings
4. hit connect button and wait for connection
5. read & write registers you need


Flashing new firmware


Flashing new firmware using Android phone is supported (with bluetooth adapter) on all EVSE DIN devices and on EVSE Wallbox devices only with “modbus firmware”. In order to flash new version of firmware bootloader mode must be enabled (last bit of the register 2005 - see the below).

Bootloader mode
If bootloader mode is activated the LED is solid on or off and it toggles when there is active communication. Bootloader mode can be turned off by changing the configuration register or it happens automatically after successful flashing of new firmware or there is a timeout of approximately 4 minutes.
When bootloader mode is activated, modbus slave address is set to 1.
The other way to enter bootloader mode is to keep analog input down when the device is booting (before powering on) for about 12 seconds (CHECK: or some more complicated way to prevent accidental bootloader turn on? CONCLUSION: if divider 1:1 used for AN => colision, result: this option disabled)
Bootloader change with board having initial revision 10: bootloader can be enabled by pulling MCLR (pin 1 PROG header) down for at least 12 seconds. This is needed for the case that software upgrade fails and there is no possibility to enable bootloader by changing the register.

Troubleshooting
If the download of a new firmware was not completed then you need to try it again, otherwise the board will not function properly. Last chance to fix badly programmed board is using PICKIT programmer (you can order PicKIT 4 on Farnell to get it fast).

How to determine firmware version?
If you power up the EVSE board and the LED is on for about 2 - 3 seconds you have Modbus firmware onboard and it is disabled. You can enable it this way NOTE#1. Firmware revision can be then read from register 1005.

Analog input control
Charging current can be changed based on analog input AN voltage (when register 2003 = 0). Minimum value is set in register 2002 and maximum in register 2000. Default supported range is 0 - 5V. Analog input is referenced to GND and is not isolated
Charging current (IPWM) for the vehicle is calculated:

IPWM = UAN / 5 * IMAX

Where UAN is the voltage measured at the input AN and IMAX is actual maximum current. Default is 32A, however it can be adjusted by settings or “current boost” / ”current limit” feature or change in configuration register.
If the resulting current is smaller than 6A then the EVSE state will change to “pilot steady 12V” and vehicle stops charing. Minimum current can be also adjusted in the register.
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

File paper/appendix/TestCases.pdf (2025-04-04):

Simulation test cases
Phase | Module | Description | Expectation | result
| Web | Incorrect input | Show hint, halt step | As expected
| | incompletely filled out | Show hint, halt step | As expected
| | EVSE in use/ Not exist/Error | Halt step | As expected
| | Shelly not available | Halt step | As expected
| | Correctly filled in, device ready | Send request to the optimizer | As expected
| | click Start directly | No Reaction | As expected
| | click Stop directly | No Reaction | As expected
Optimizer | Disconnect with the optimizer | Wait for the connection | As expected
| Connect with the Opt. Again | Connect again | As expected
| Error in the optimizer | Halt step | As expected
| Succeeded | Charge-Plan receive | As expected
Vehicle | No car plugged in | Halt step | As expected
| Car plugged in | Charging ready | As expected
Button (Web) | Click Start without filling in | No Reaction | As expected
| Click Stop without filling in | No Reaction | As expected
| Click Reset-Error without Error | No Reaction | As expected
| Status error, click Start | No Reaction | As expected
| Status error, click Stop | No Reaction | As expected
| Status error, Click Reset-Error | Error reset, contact the administrator | As expected
| Steps finished, status normal | Charging ready | As expected
Beginning of charging | EVSE | No car plugged in | Not allowed to start charging | As expected
| | Error | Not allowed to start charging | As expected
| | Status available | Charging ready | As expected
Shelly | Error | Not allowed to start charging | As expected
| Status available | Charging ready | As expected
Start | Has not clicked start button | Wait, initialize | As expected
| Start clicked | Adjust schedule, lock, EVSE self-test | As expected
EVSE Selftest | Succeed in self-test | Charging ready, wait | As expected
| Self-test failed | Error, Halt step | As expected

In charging

EVSE | Error | Stop Charging | As expected
Shelly | Error | Stop Charging | As expected
User | Click stop button | Stop Charging | As expected
| Do not stop, resend request | Request rejected | As expected
| Stop, Send request again | Start from the top | As expected
| start again | Continue executing, no effect | As expected
Opt. | Disconnect with the optimizer | Continue executing, no effect | As expected
| Connected with the optimizer again | Continue executing, no effect | As expected
Calibration | Connected with the optimizer | Periodic calibration | As expected
| Disconnected with the optimizer | Continue executing, no effect | As expected
Finish charging | Schedule list is empty | Stop Charging | As expected
| Energy fully charged | Stop Charging | As expected

Before
charging

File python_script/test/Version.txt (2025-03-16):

VSVersionInfo(
    ffi=FixedFileInfo(
        filevers=(0, 1, 16, 0),
        prodvers=(0, 1, 16, 0),
        mask=0x0000003F,
        flags=0x00000000,
        OS=0x00040004,
        fileType=0x00000001,
        subtype=0x00000000,
    ),
    kids=[
        StringFileInfo([
            StringTable(u'040904B0', [
                StringStruct(u'FileVersion', u'0.1.16.0'),
                StringStruct(u'ProductVersion', u'0.1.16.0'),
                StringStruct(u'ProductName', u'Modbus_Shelly_Simulator'),
                StringStruct(u'CompanyName', u'ADP2024'),
                StringStruct(u'OriginalFilename', u'Modbus_Shelly_Simulator.exe'),
                StringStruct(u'FileDescription', u'A simulation testing software for pre-high-voltage testing.')
            ])
        ]),
        VarFileInfo([
            VarStruct('Translation', [
                0x0409, 0x04B0
            ])
        ])
    ]
)

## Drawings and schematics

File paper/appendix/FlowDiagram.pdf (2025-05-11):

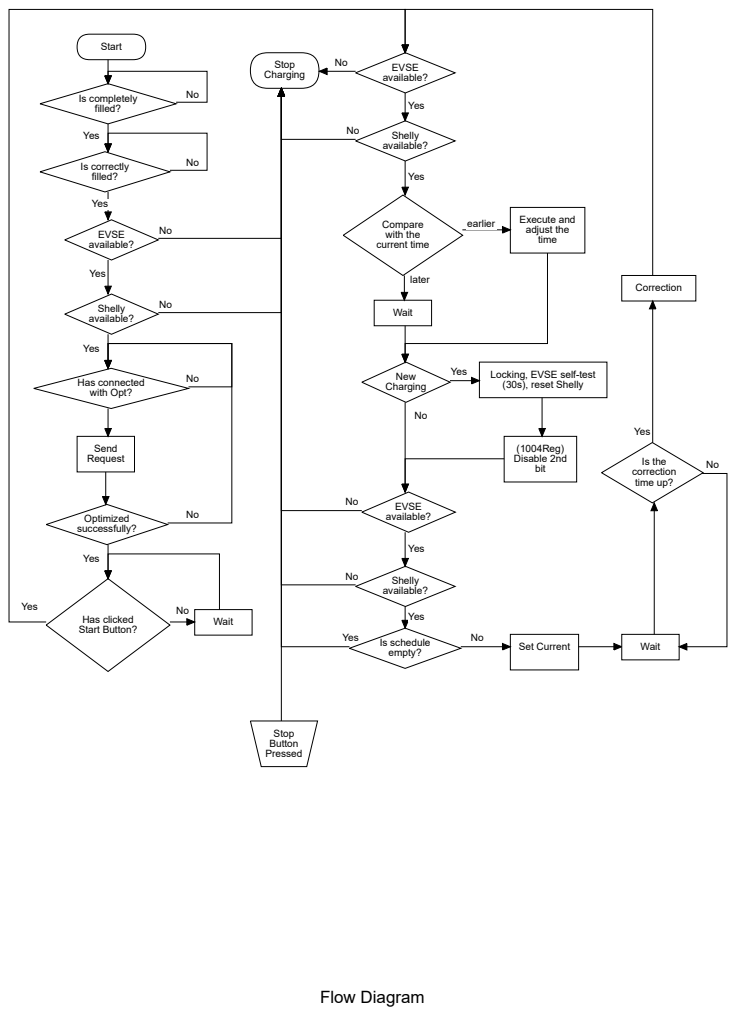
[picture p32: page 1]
Is completely filled?; Is correctly filled?; EVSE available?; Has connected with Opt?; Optimized successfully?; New Charging; Shelly available?; Compare with the current time; Has clicked Start Button?; Send Request; Wait; Execute and adjust the time; Is schedule; empty?; Set Current; (1004Reg) Disable 2nd; bit; Is the; correction time up?; Correction; Yes; later; earlier; Start; Stop Charging; Stop Button Pressed; Flow Diagram

Locking, EVSE self-test
(30s), reset Shelly

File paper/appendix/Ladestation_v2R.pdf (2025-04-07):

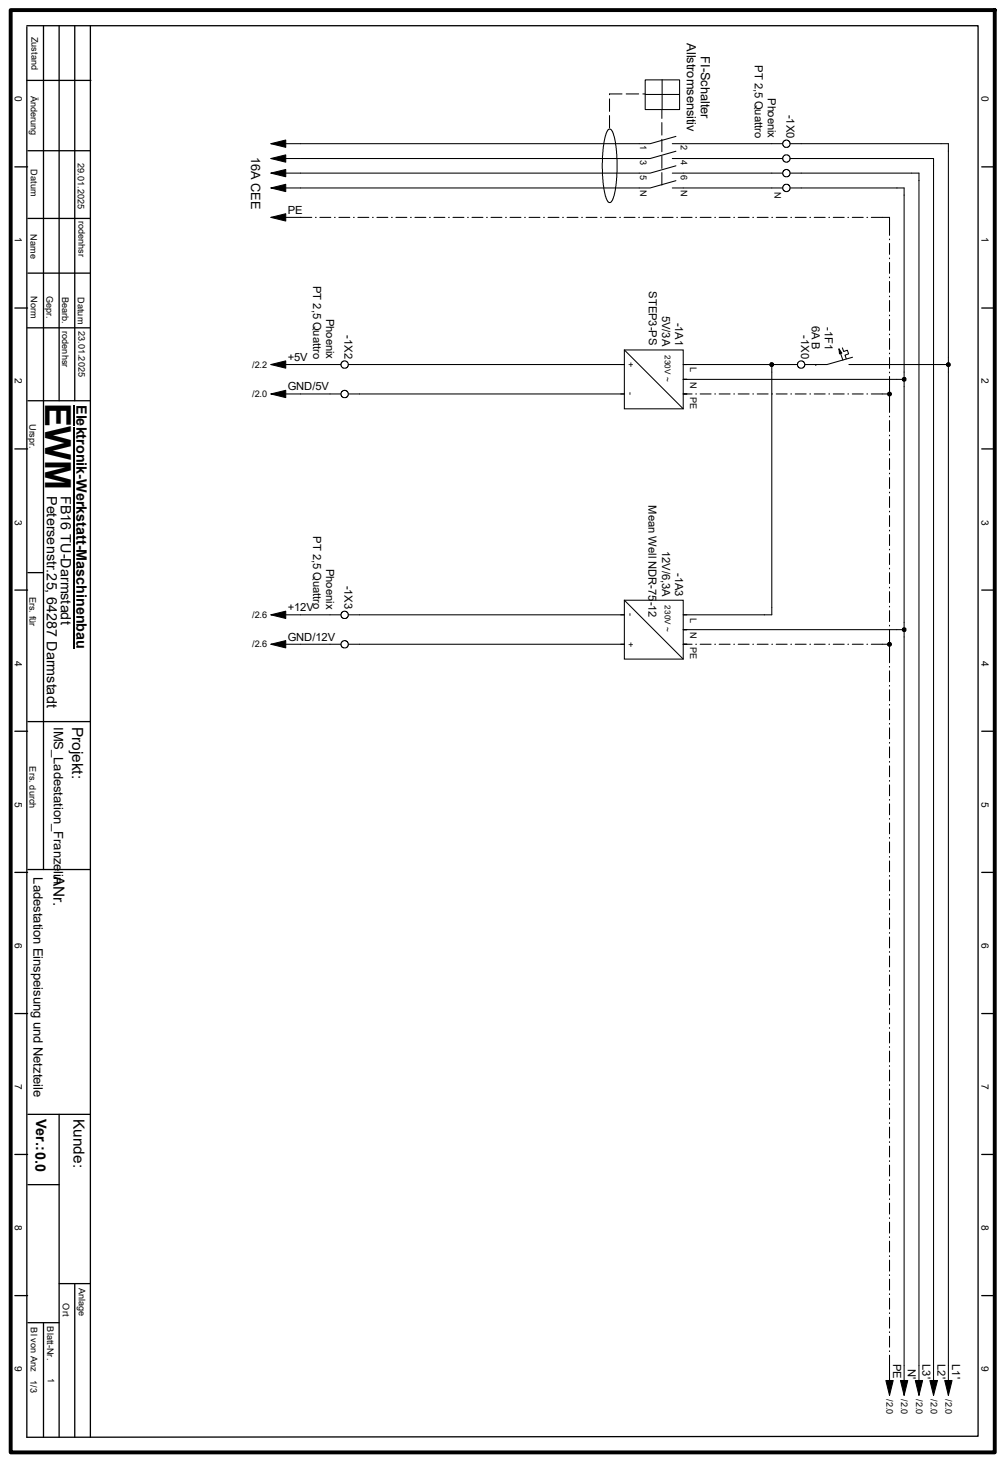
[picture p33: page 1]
Phoenix; PT 2,5 Quattro; PT 2,5 Quattro +5V /2.2; STEP3-PS; GND/5V /2.0; PT 2,5 Quattro +12V; GND/12V /2.6; Allstromsensitiv FI-Schalter; 16A CEE; Ort; Anlage; ANr.; Ers. durch; Ers. für; Datum; 1/3Name; Gepr.; Bearb.; Zustand; DatumÄnderung; FB16 TU-Darmstadt; Norm Urspr.; rodenhsr; Ver.:

23.01.2025 29.01.2025 Elektronik-Werkstatt-Maschinenbau

rodenhsr Projekt: Kunde:

Ladestation Einspeisung und Netzteile 0.0 EWM IMS_Ladestation_Franzelin

Blatt-Nr. Petersenstr.25, 64287 Darmstadt

Mean Well NDR-75-12

Bl von Anz

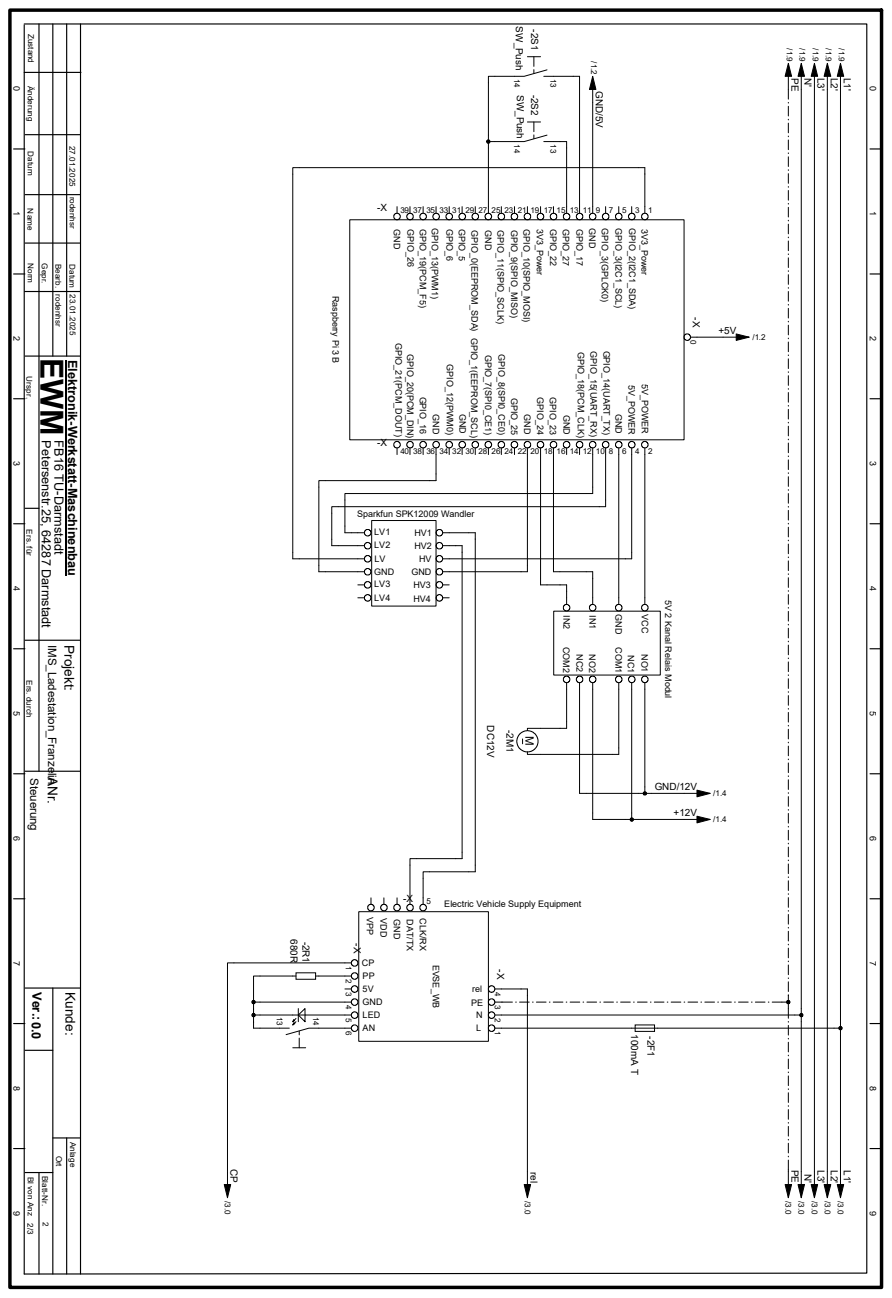
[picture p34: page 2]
SW_Push; GND/5V /1.2; GND/12V; rel; GPIO_25; GPIO_8(SPI0_CE0); GPIO_15(UART_RX); 5V_POWER; 3V3_Power; GPIO_21(PCM_DOUT); GND; GPIO_16; GPIO_13(PWM1); GPIO_5; GPIO_23; GPIO_19(PCM_F5); VPP; VDD; GPIO_7(SPI0_CE1); GPIO_11(SPIO_SCLK); COM1; Sparkfun SPK12009 Wandler; GPIO_6; GPIO_27; GPIO_26; GPIO_18(PCM_CLK); GPIO_22; GPIO_20(PCM_DIN); GPIO_10(SPIO_MOSI); GPIO_2(I2C1_SDA); VCC; GPIO_12(PWM0); COM2; Raspberry Pi 3 B; GPIO_0(EEPROM_SDA); GPIO_9(SPIO_MISO); GPIO_3(GPLCK0); GPIO_3(I2C1_SCL)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

23.01.2025 27.01.2025 Elektronik-Werkstatt-Maschinenbau

rodenhsr Projekt: Kunde:

Blatt-Nr. Petersenstr.25, 64287 Darmstadt

5V 2 Kanal Relais Modul

Electric Vehicle Supply Equipment

Bl von Anz

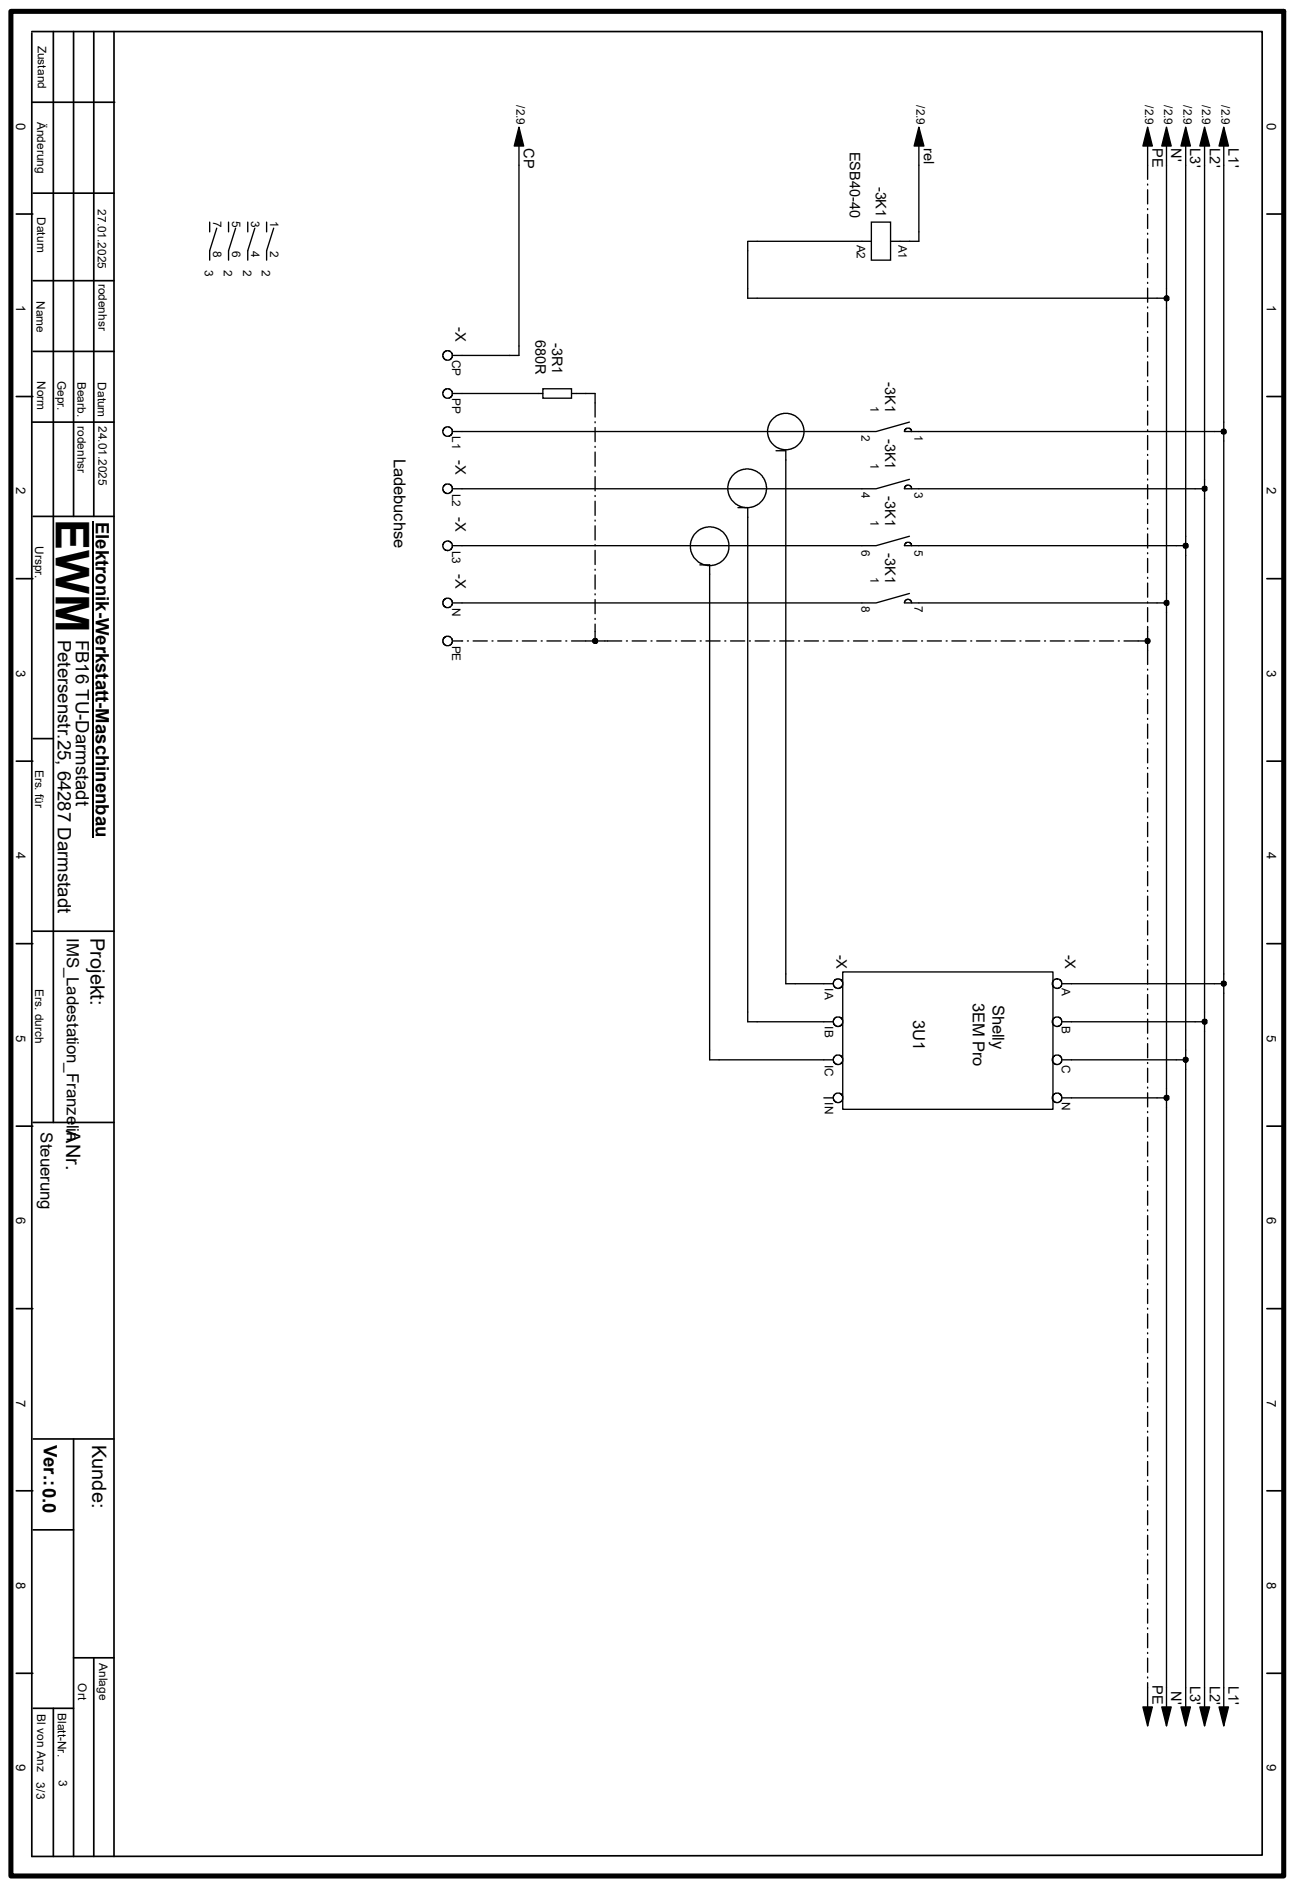
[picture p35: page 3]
rel; ESB40-40; Ladebuchse; 3EM Pro Shelly; Ort; Anlage; ANr.; Ers. durch; Steuerung 0.0 EWM IMS_Ladestation_Franzelin; Ers. für; Datum; 3/3Name; Gepr.; Bearb.; DatumÄnderung; FB16 TU-Darmstadt; Norm Urspr.; rodenhsr; Ver.:

24.01.2025 27.01.2025 Elektronik-Werkstatt-Maschinenbau

rodenhsr Projekt: Kunde:

Blatt-Nr. Petersenstr.25, 64287 Darmstadt

Bl von Anz

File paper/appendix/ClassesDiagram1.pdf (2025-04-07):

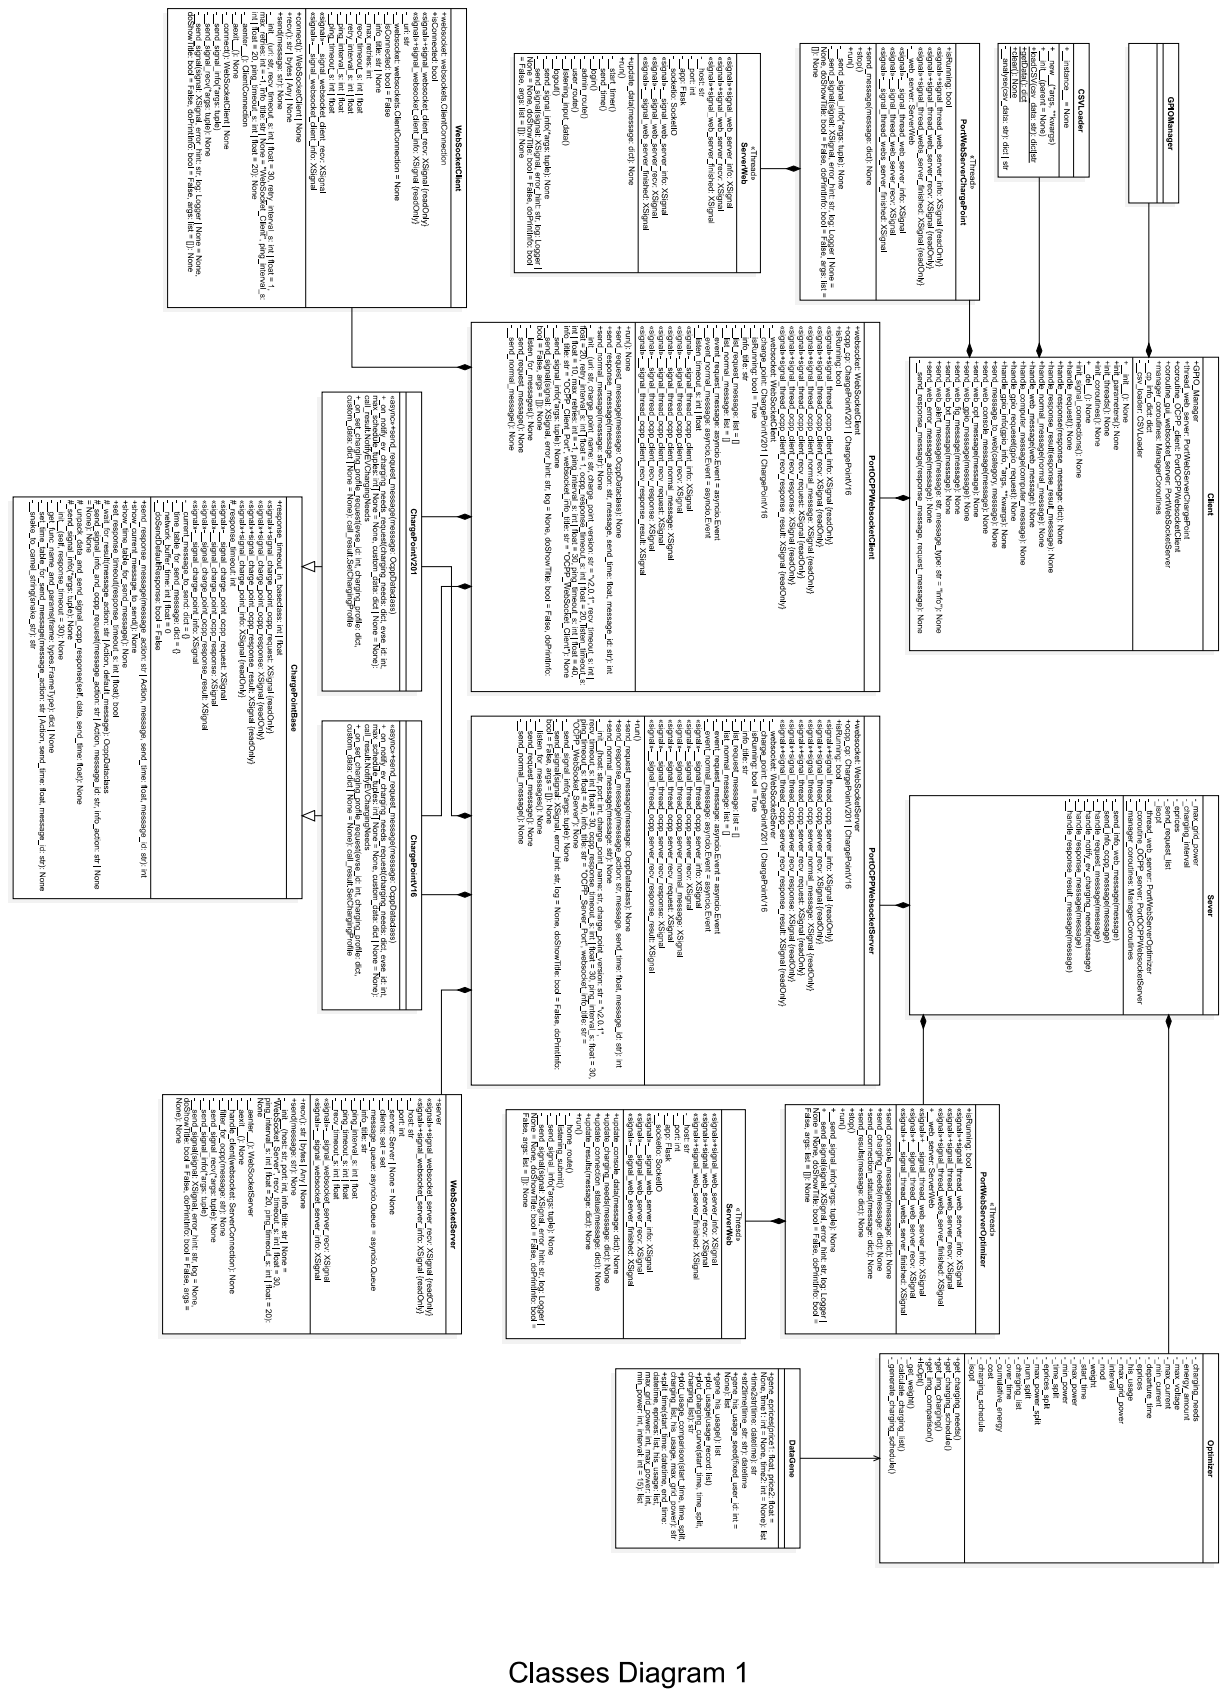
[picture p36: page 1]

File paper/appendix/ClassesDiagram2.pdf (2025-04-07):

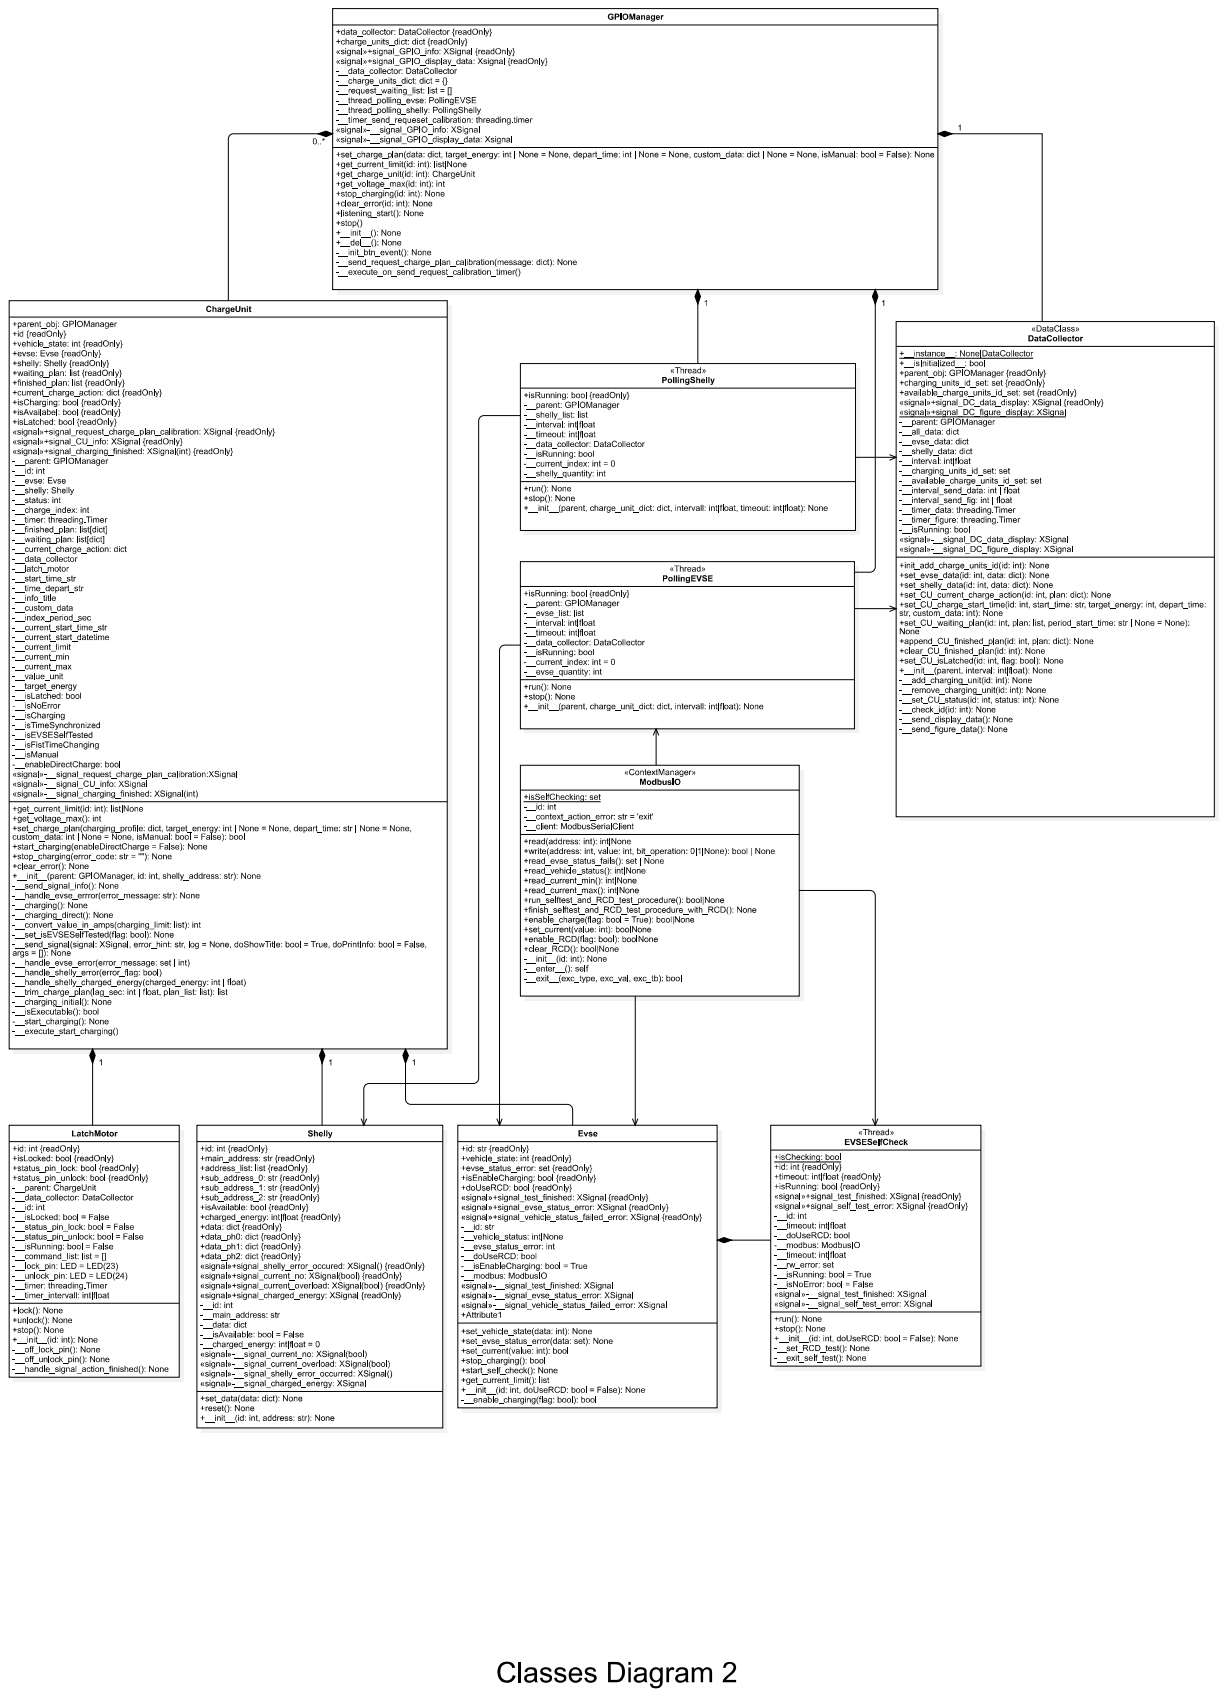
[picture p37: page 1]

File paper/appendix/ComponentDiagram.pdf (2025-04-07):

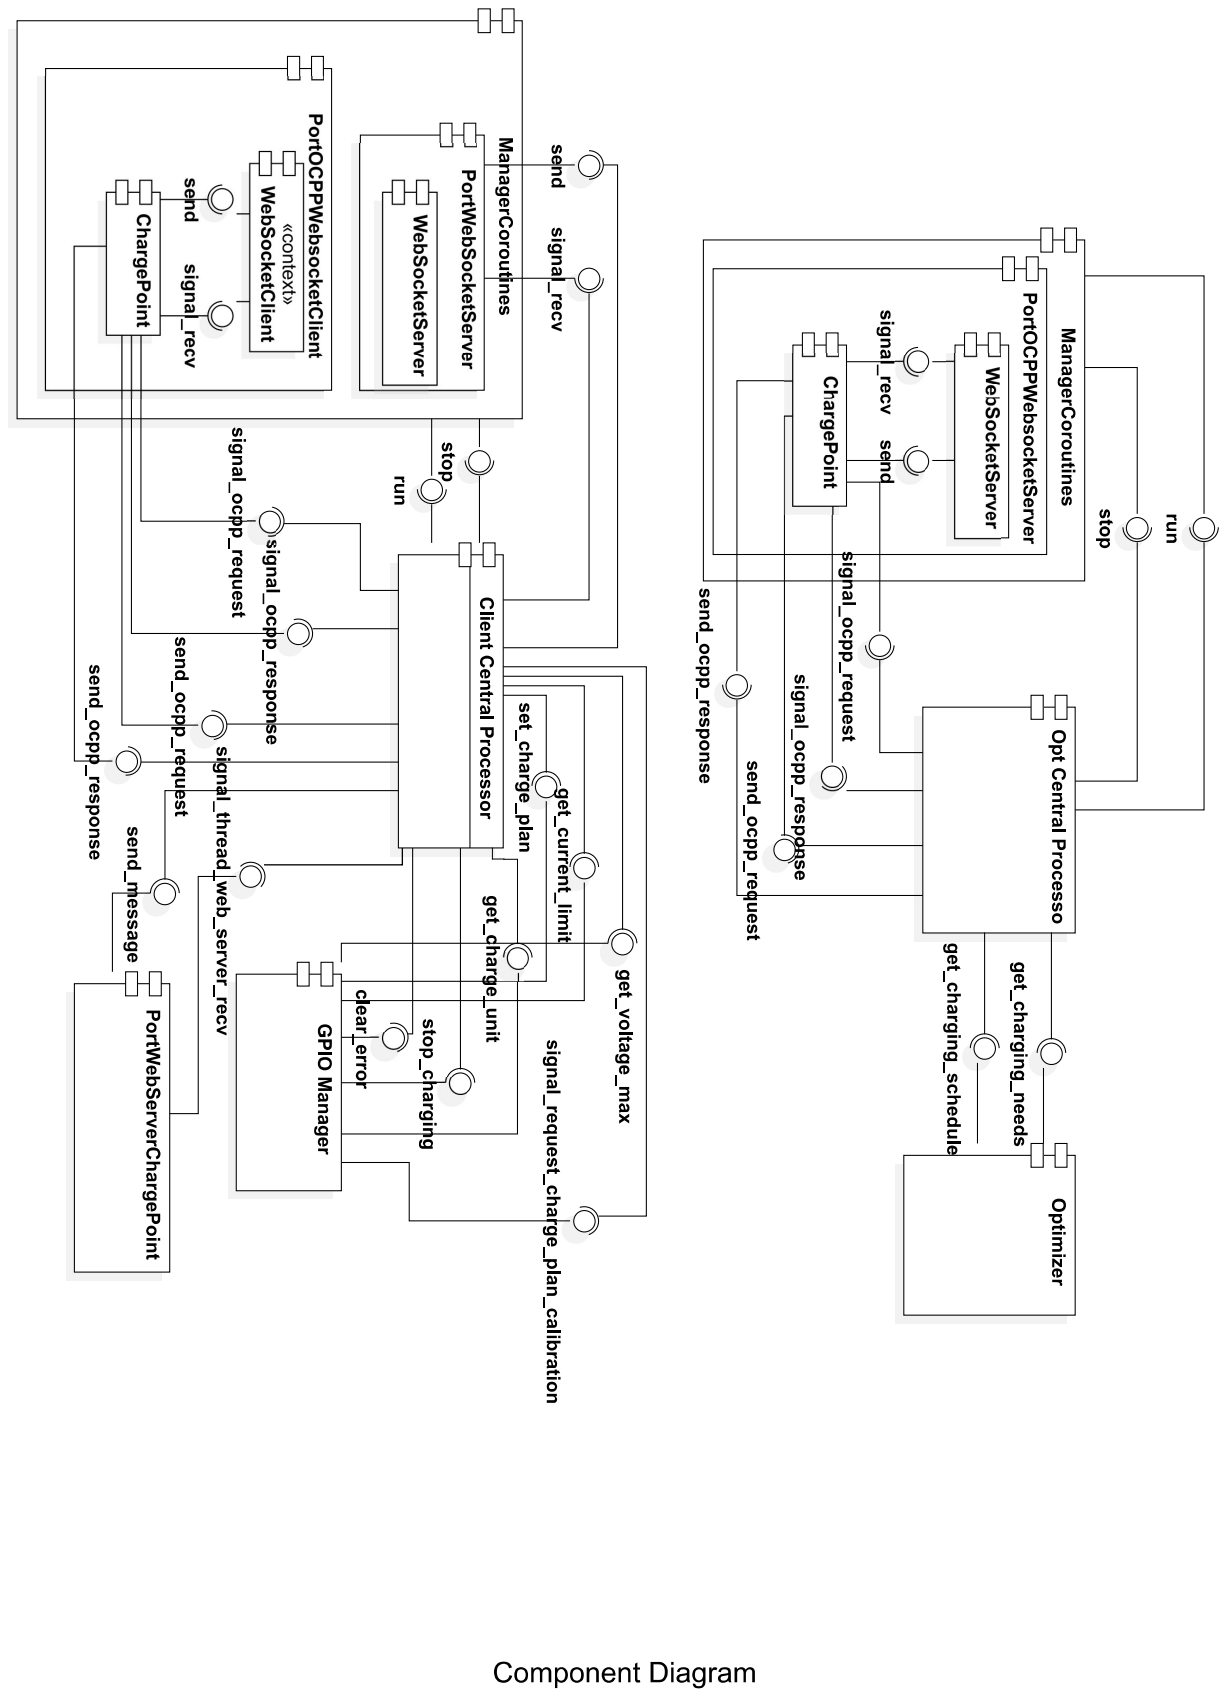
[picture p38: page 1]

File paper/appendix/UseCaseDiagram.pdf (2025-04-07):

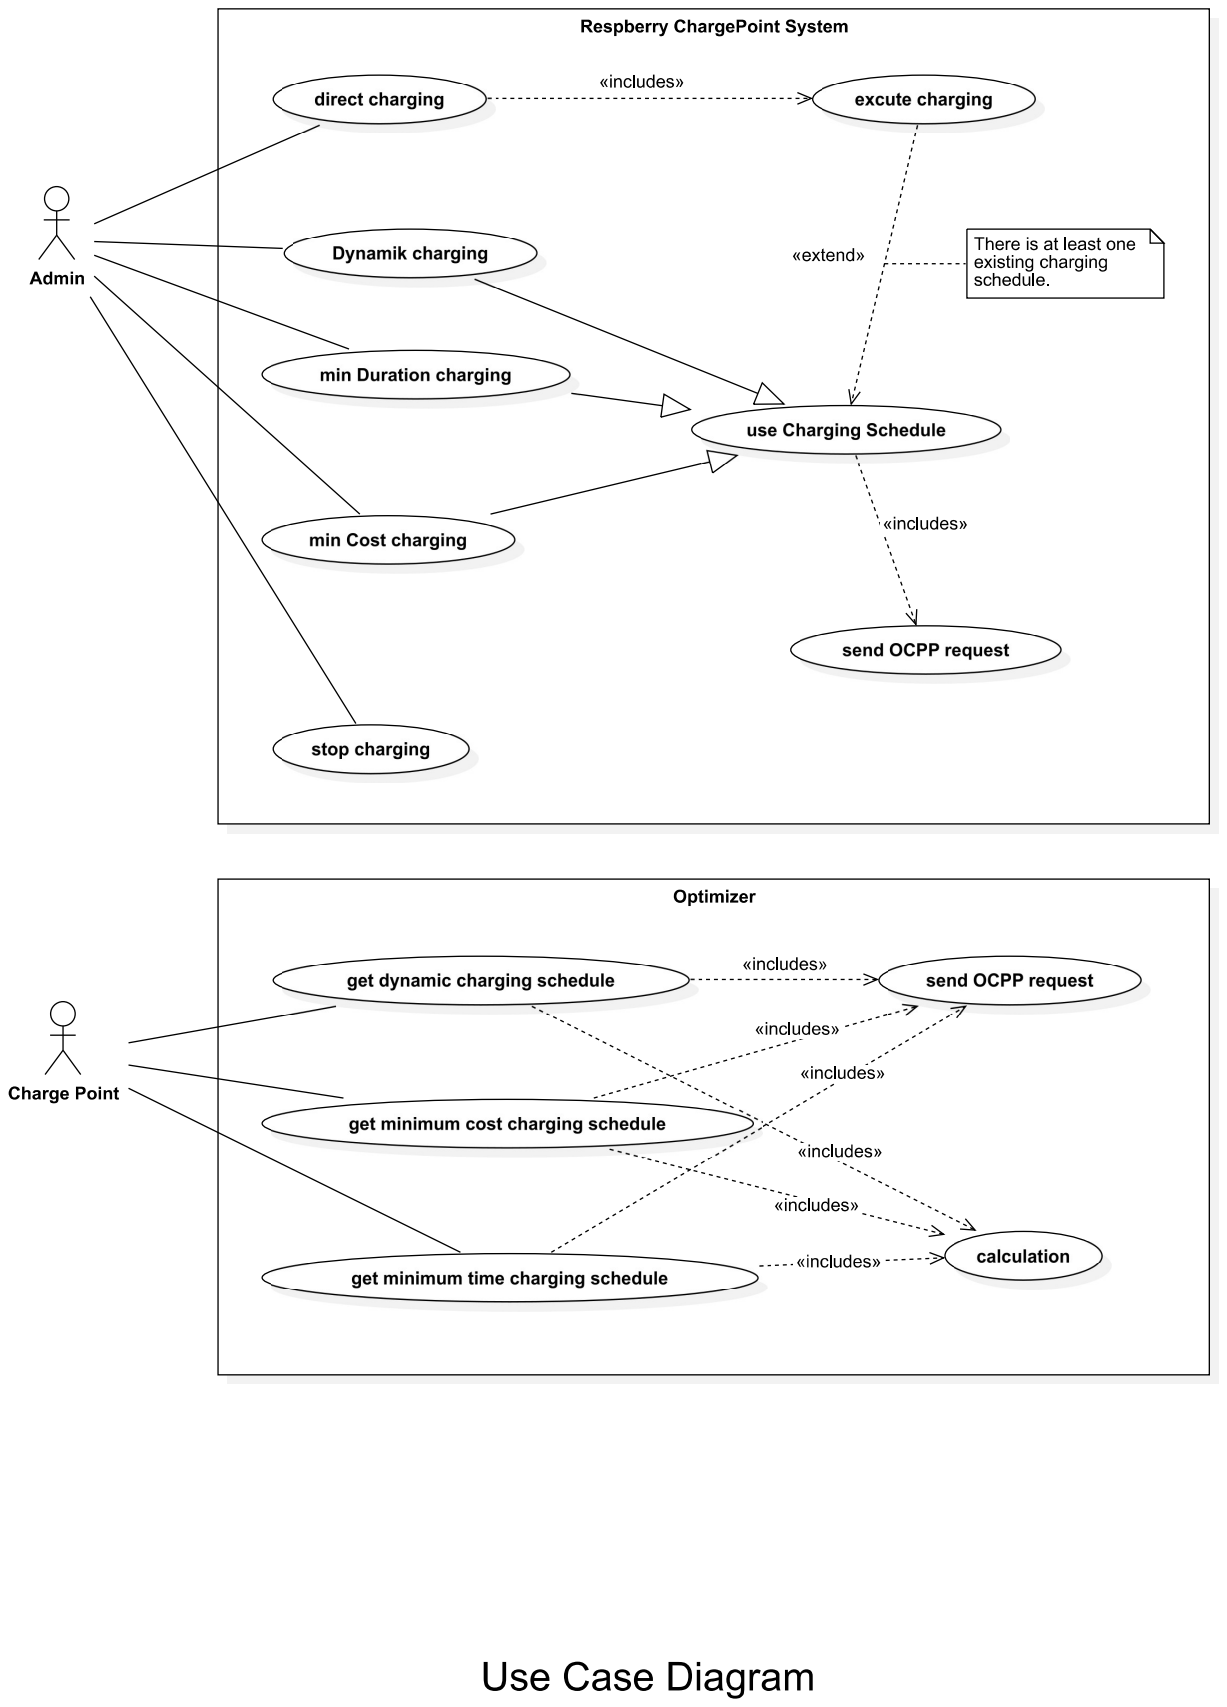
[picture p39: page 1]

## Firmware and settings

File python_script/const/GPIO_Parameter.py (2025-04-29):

"""
GPIO 枚举类


"""
from const.Analog_Define import AnalogDefine
from tools.check_func import import_data


class EVSERegAddress(AnalogDefine):
    CONFIGURED_AMPS = 1000
    AMPS_OUTPUT = 1001
    VEHICLE_STATE = 1002
    CURRENT_MAX = 1003
    TURN_OFF_SELFTEST_OPERATION = 1004  # turn off charging | self test operation
    FIRMWARE_REVISION = 1005
    EVSE_STATE = 1006
    EVSE_STATUS_FAILS = 1007
    TIMEOUT_ERROR = 1008
    TIMEOUT_SELFTEST = 1009
    # ...
    DEFAULT_AMPS = 2000
    SLAVE_ADDRESS = 2001
    CURRENT_MIN = 2002
    ANALOG_INPUT_CONFIG = 2003
    AMPS_SETTINGS = 2004
    CHARGE_OPERATION = 2005
    CURRENT_SHARING_MODE = 2006
    PP_DETECTION = 2007
    # ...
    BOOTLOADER_FIRMWARE_REVISION = 2009
    AMPS1 = 2010
    AMPS2 = 2011
    AMPS3 = 2012
    AMPS4 = 2013
    AMPS5 = 2014
    AMPS6 = 2015
    AMPS7 = 2016
    AMPS8 = 2017


_dct = import_data()


class GPIOParams(AnalogDefine):
    VENDOR_ID = 'Darmstadt'
    MESSAGE_SEND_INTERVAL = 60  # seconds
    CHARGE_UNITS = [
        # (EVSE_Id, Shelly_main_url)
        (1, 'shellypro3em-2cbcbbb2e0b8.local'),
        # (1, '172.18.25.49:6666'),
        # (1, '172.18.20.152:6666'),
        # (1, 'http://192.168.124.9:6666'),
        # (1, 'http://130.83.148.29:6666'),

        # (0, '192.168.1.100'),
        # (1, 'url1'),
    ] if 'charge_units' not in _dct else _dct['charge_units']
    DO_USE_RCD: bool = False
    MAX_VOLTAGE = 220 if 'max_voltage' not in _dct else _dct['max_voltage']
    MAX_SHELLY_RETRY = 5 if 'max_shelly_retry' not in _dct else _dct['max_shelly_retry']
    ASSUMED_PHASE = 3 if 'assumed_phase' not in _dct else _dct['assumed_phase']
    SELF_CHECK_TIMEOUT = -31 if 'self_check_timeout' not in _dct else _dct['self_check_timeout']
    """ EVSE 自检时间, 单位: 秒. 该值必须 >=30 秒, 否则自检将不会启动 """
    LETCH_MOTOR_RUNTIME = 1 if 'letch_motor_runtime' not in _dct else _dct['letch_motor_runtime']
    """ 栓电机运行时间, 单位: 秒. 该值必须大于0秒, 否则电机将不会启动 """
    CALIBRATION_PERIOD = 60 if 'calibration_period' not in _dct else _dct['calibration_period']
    """ 校准周期, 单位: 秒. 该值必须大于0秒, 否则校准将不会启动 """
    POLLING_EVSE_INTERVAL = 1 if 'polling_evse_interval' not in _dct else _dct['polling_evse_interval']
    """ 轮询 EVSE 间隔, 单位: 秒. 该值必须大于0秒 """
    POLLING_SHELLY_INTERVAL = 1 if 'polling_shelly_interval' not in _dct else _dct['polling_shelly_interval']
    """ 轮询 Shelly 间隔, 单位: 秒. 该值必须大于0秒 """
    POLLING_SHELLY_TIMEOUT = 10 if 'polling_shelly_timeout' not in _dct else _dct['polling_shelly_timeout']
    """ Shelly 超时时间, 单位: 秒. 该值必须大于0秒 """
    DATACOLLECTOR_DATA_INTERVAL = 1 if 'datacollector_data_interval' not in _dct else _dct['datacollector_data_interval']
    """ 文字数据发送间隔, 单位: 秒. 该值必须大于0秒 """
    DATACOLLECTOR_FIG_INTERVAL = 1 if 'datacollector_fig_interval' not in _dct else _dct['datacollector_fig_interval']
    """ 图像数据发送间隔, 单位: 秒. 该值必须大于0秒 """
    REQUEST_INTERVAL = 1
    """ 请求间隔, 单位: 秒. 该值必须大于0秒 """
    BOUNCETIME = 200
    """ 树莓派按钮检测防抖时间 """
    EVSE_WRITE_RETRY = 10 if 'evse_write_retry' not in _dct else _dct['evse_write_retry']
    """ EVSE 写入重试次数 """
    CHARGING_STABLE_COUNTDOWN = POLLING_EVSE_INTERVAL * 10 if 'charging_stable_countdown' not in _dct else _dct['charging_stable_countdown']
    WATCHING_REGISTERS = [
        EVSERegAddress.CONFIGURED_AMPS,
        EVSERegAddress.AMPS_OUTPUT,
        EVSERegAddress.VEHICLE_STATE,
        EVSERegAddress.CURRENT_MAX,
        EVSERegAddress.TURN_OFF_SELFTEST_OPERATION,
        EVSERegAddress.EVSE_STATE,
        EVSERegAddress.DEFAULT_AMPS,
        EVSERegAddress.CURRENT_MIN,
    ]
    WATCHING_REGISTERS_GROUP = [
        (EVSERegAddress.CONFIGURED_AMPS, 7),
        (EVSERegAddress.DEFAULT_AMPS, 3)
    ]


class ResultFlag(AnalogDefine):
    SUCCESS = 0
    FAIL = 1


class VehicleState(AnalogDefine):
    READY = 1  # 准备就绪, 可以开始充电
    EV_IS_PRESENT = 2  # 车辆已插入
    CHARGING = 3  # 充电中
    CHARGING_WITH_VENTILATION = 4  # 充电中, 需要通风
    FAILURE = 5  # 故障
    CRITICAL = 666  # 严重故障


class REG1006(AnalogDefine):
    ACTIVE = 0
    STEADY = 1
    PWM_GENERATED = 2
    OFF = 3


class EVSEErrorInfo(AnalogDefine):
    RELAY_OFF = 'Relay Off'
    RELAY_ON = 'Relay On'
    DIODE_CHECK_FAIL = 'diode Check Fail'
    VENT_REQUIRED_FAIL = 'Vent Required Fail'
    WAITING_FOR_PILOT_RELEASE = 'Waiting For Pilot Release'
    RCD_CHECK_ERROR = 'RCD Check Error'
    RCD_CHECK_FAILED = 'RCD Check Failed'
    READ_ERROR = 'Read Error'
    WRITE_ERROR = 'Write Error'
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

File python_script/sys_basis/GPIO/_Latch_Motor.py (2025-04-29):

from __future__ import annotations
import threading

from ._import_modbus_gpio import *
from const.GPIO_Parameter import *
from const.Const_Parameter import *

if 0:
    from ._Data_Collector import DataCollector
    from ._Charge_Unit import ChargeUnit

_info = Log.GPIO.info


class LatchMotor:
    """
    数值默认正数是上锁
    """

    def __init__(self, parent: ChargeUnit, id: int) -> None:
        self.__id: int = id
        self.__parent: ChargeUnit = parent
        self.__data_collector: DataCollector = parent.parent_obj.data_collector
        self.__isLocked: bool = False  # 锁的状态, 是否是上锁状态
        self.__isRunning: bool = False  # 是否电机正在运行, 用于避免电机转动时, 动作冲突
        self.__command_list: list = []  # 存储命令的列表
        self.__status_pin_lock: bool = False  # 电机上锁控制引脚的状态, 可表示电机是否在正转
        self.__status_pin_unlock: bool = False  # 电机解锁控制引脚的状态, 可表示电机是否在反转
        self.__lock_pin: LED = LED(RaspPins.BCM_PIN_23)  # 电机上锁控制引脚
        self.__unlock_pin: LED = LED(RaspPins.BCM_PIN_22)  # 电机解锁控制引脚
        self.__timer: threading.Timer = threading.Timer(99, self.__off_lock_pin)
        self.__timer.name = 'LatchMotor'
        self.__timer_intervall: int | float = GPIOParams.LETCH_MOTOR_RUNTIME  # 引脚状态转换的时间
        self.unlock()  # 初始化时解锁

    @property
    def id(self) -> int:
        return self.__id

    @property
    def isLocked(self) -> bool:
        return self.__isLocked

    @property
    def status_pin_lock(self) -> bool:
        return self.__status_pin_lock

    @property
    def status_pin_unlock(self) -> bool:
        return self.__status_pin_unlock

    def lock(self) -> None:
        """
        上锁操作
        """
        if self.__isRunning:
            self.__command_list.append(1)  # 正数表示上锁
        if self.__isLocked or self.__timer_intervall <= 0:
            return
        self.__unlock_pin.off()
        self.__status_pin_unlock = False
        self.__lock_pin.on()
        self.__status_pin_lock = True
        self.__timer = threading.Timer(self.__timer_intervall, self.__off_lock_pin)
        self.__timer.name = 'LatchMotor'
        self.__timer.start()

    def unlock(self) -> None:
        """
        解锁操作
        """
        if self.__isRunning:
            self.__command_list.append(-1)  # 负数表示解锁
        if not self.__isLocked or self.__timer_intervall <= 0:
            return
        self.__unlock_pin.on()
        self.__status_pin_unlock = True
        self.__lock_pin.off()
        self.__status_pin_lock = False
        self.__timer = threading.Timer(self.__timer_intervall, self.__off_unlock_pin)
        self.__timer.name = 'LatchMotor'
        self.__timer.start()

    def stop(self) -> None:
        self.__lock_pin.off()
        self.__unlock_pin.off()
        # 缺少安全措施, 比如锁在一半停下了, 可以置默认操作, 上锁或解锁

    def __off_lock_pin(self) -> None:
        """
        一段时间后将上锁正转引脚置否, 停止电机运转
        """
        self.__lock_pin.off()
        self.__status_pin_lock = False
        self.__isLocked = True
        self.__handle_signal_action_finished()

    def __off_unlock_pin(self) -> None:
        """
        一段时间后将解锁反转引脚置否, 停止电机运转
        """
        self.__unlock_pin.off()
        self.__status_pin_unlock = False
        self.__isLocked = False
        self.__handle_signal_action_finished()

    def __handle_signal_action_finished(self) -> None:
        """
        处理动作完成信号, 检查是否有后续连续操作
        """
        self.__data_collector.set_CU_isLatched(id=self.id, flag=self.__isLocked)
        _info(f'Action finished, isLatched: {self.__isLocked}')
        setattr(self.__parent, f'_{self.__parent.__class__.__name__}__isLatched', self.__isLocked)
        if len(self.__command_list) == 0:
            return
        command = self.__command_list.pop(0)
        if command > 0:
            self.lock()
        else:
            self.unlock()

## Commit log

2024-12-03 更新快捷方式忽略
2024-12-03 上传开发工具和代码规范
2024-12-03 占位文件
2024-12-03 上传基础py文件
2024-12-03 删除访问方法
2024-12-03 定义示例
2024-12-08 添加工具，与开发的代码无关，用于帮助开发
2024-12-08 新增数据类(模板)
2024-12-08 更新数据类的初始模板
    修改了错误的继承类名
    修改了import方式，以便ide可以识别继承方法
2024-12-08 新增核对的常量
    Valid为校验的枚举类(修改保护，重复命名保护)， All_Standard为原数据
2024-12-08 更改方法
    更改为静态方法
2024-12-08 更改标点符号
2024-12-08 更新.gitignore
    添加对pycharm的ignore
2024-12-08 更正函数注解错误
    generate(id_token: str, ...)
    更正为：
    generate(id_token: dict, ...)
2024-12-08 更正修改为静态方法时，未删去self的错误
2024-12-08 更改文件夹名称
    Generator_Message_V1_6 更改为 V1_6
    Generator_Message_V2_0_1 更改为 V2_0_1
    避免不必要的细化名称，缩短import的长度
2024-12-08 更正相对引入错误
2024-12-09 新增异步计时器
2024-12-09 新增 websocket的上下文管理器 服务器与客户端
2024-12-09 新增 含有Ocpp的测试脚本
2024-12-09 更新 模板数据类v16
    引入数据标准类型 call 模块
2024-12-09 更新 模板数据类v201
    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
2024-12-09 修复引入bug
2024-12-09 修改注释格式
2024-12-09 优化器思路构建
    添加优化器demo和思路文件
2024-12-09 更新数据生成类
2024-12-09 更新注释，更新函数名等
2024-12-09 更新测试
2024-12-09 Squashed commit of the following:
    commit 16752bcf448896a5823b88c08dab06b37c0ff25c
    Author: zchasing <zchasing97@gmail.com>
    Date: Mon Dec 9 17:38:59 2024 +0100
    修改文件路径，更新部分数据类
    挪动Optimize文件夹位置
    更新数据类NotifyEVChargingScheduleRequest和NotifyEVChargingNeedsRequest
    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
2024-12-09 更新开发工具，修改创建逻辑
2024-12-09 更新 模块数据类 V1_6
    更新模块结构，完善引入
2024-12-09 更新 模块数据类 V2_0_1
    更新 模块结构，完善引入
2024-12-09 更正引入错误
    将from ocpp.v201.enums import *中的v201更正为：v16
2024-12-09 Update _AuthorizeRequest.py
    更新 import
    更新 变量注解
    更新 注释，尤其是含有枚举类的部分
    统一格式，取值范围全部使用[, ] 或 [ - ], 前者用于数值，后者用于字符串长度
2024-12-09 Update _AuthorizeResponse.py
    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
2024-12-09 更新测试文件
2024-12-11 更新_NotifyEVChargingScheduleRequest.py
    完善_NotifyEVChargingScheduleRequest.py
2024-12-12 更新测试文件
    主要对服务器的充电桩基类的功能测试进行更新
2024-12-12 修改bug
    修复执行self.__check_file()前未定义 self.__default_setting_dict
2024-12-12 新增客户端充电桩的文件
2024-12-12 新增服务端充电桩的文件
2024-12-12 Update README.md
    更新谷歌表格链接
2024-12-12 标点符号更新
    小更新，更新中文标点符号
2024-12-12 上传架构图
2024-12-12 更新多个Response.py
    更新NotifyEVChargingNeedsResponse和NotifyEVChargingScheduleResponse
    修正AuthorizeResponse
2024-12-12 合并两个文件夹及类
    将服务端和客户端进行合并
    更改了服务端的对外方法
2024-12-12 完善架构及基类
    新增解包数据发送信号的方法，用于接收响应
    新增发送请求方法
    增添方法注释，类注释
2024-12-12 更新WebSocket客户端
    新增类内信号 signal_recv
    新增发送接收信号函数
    将print统一改用发送信号函数
2024-12-12 Update WebSocket_Server.py
    更新WebSocket客户端
    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
2024-12-12 更新 模块数据类 V1_6
    完善引入
2024-12-12 更新 模块数据类 V2_0_1
    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
2024-12-12 标点符号修改
2024-12-13 更正了信号定义，并增加对信号的保护
2024-12-13 更新注释
2024-12-14 更新文件
    新增注释
    新增变量注解
    更正信号定义，并增加保护
    新增信息信号
    新增初始化变量检查
    分离信号发送的方法
2024-12-14 Update WebSocket_Server.py
    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
2024-12-14 更正发送方法，增加基础方法的参数
2024-12-14 更新注释，添加网络延时的设置
2024-12-14 更新注释，在通知信号中添加忽略响应的内容
2024-12-14 更新注释，更正字符转换的bug
2024-12-14 新增ocpp_WebSocket端口客户端线程
    未测试，且send_response_message方法仍需完善
    未写注释
2024-12-14 新增响应发送结果信号
2024-12-14 Update Thread_OCPP_Client_Port.py
    新增响应结果信号，解决了响应结果无反馈的问题
    新增运行标志，确保关闭线程时可以顺利进行
2024-12-14 添加优化器数据类
    添加ChargingScheduleRequest和ChargingNeedsRequest.py
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2024-12-14 Update Thread_OCPP_Client_Port.py
    新增注释和变量注解
    更正send_response_message的形参
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2024-12-17 更新服务器
    增加输出信号函数
    修改路由器，拆分为三个，用户、管理员、登录
    新增网页数据更新
    新增时钟功能
    新增监听器功能，监听网页输入
    新增登出功能
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2024-12-25 更正生成器代码问题
    更正主要问题为：
    1. 必要参数与可选参数的混淆问题
    2. 字典数据的键名混乱问题
    3. 类型中any的标识问题
    4. 枚举类的属性错误问题
    5. 标点符号修改为英文
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2025-01-03 更新ocpp Websocket端口
    新增对一般消息的处理，扩大了接收消息的范围，当消息不是以[开头，则将通过signal_thread_ocpp_***_normal_message向外传递
    新增发送一般消息的函数，但消息不得以[开头，否则无法发送
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2025-01-03 更新 模块数据类 V1_6
    更改 注释缩进
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2025-01-04 已删除 ".\dev\V201生成器模版" 文件夹, 模板文件已在项目文件夹中更新
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2025-01-06 Create 新建 Python File.py
2025-01-06 Create 新建 Python File (2).py
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2025-01-10 Update Logger.py
    增加 日志合集文件夹 Log
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2025-01-10 EVSE部分基本功能
    EVSE_manager往下的逻辑都能用，但是modbus读写的问题，得在硬件上，或者在模拟软件上测试。
    shelly还没写
    GPIOmanager还没写
    [GPIO_Parameter.py, _Decorator_check_flag.py, _EVSE_manager.py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]
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2025-01-13 更新Websocket注释以及修正代码
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2025-01-17 改了大部分的结构
    现在应该可以用字典管理多个evse和shelly的控制和数据了。
    shelly现在设置的是只要开启线程就会通过信号更新GPIOmanager的data_dict的数值（5秒一次），但是EVSE数据，包括充电时间等数据，只有在设置电流时会更新，跟新时间是根据充电周期来的，这里的逻辑需要之后再确认
    留了get_GPIO_data的方法可以得到这个字典，但是我没有设置信号往外发。
    还有各种报错信号的处理之后有时间再改
2025-01-18 Update _GPIO_Manager.py
    归还evse id
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2025-01-19 更新优化器
    优化器主函数逻辑更新
    优化器添加生成图片函数
    迁移data_gene类位置
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2025-01-21 调整结构
    EVSEmanager现在用一个线程等待EV，EV连接后线程结束，发送第一个数据，同时关闭这个等待线程，打开基本上相同的vehicle state线程
    新建了一个pillar manager，主要任务是执行charging schedule，实例化evse和shelly
    todo：
    GPIO manager， Pillar manager， EVSE, shelly之间的信号传递还没有改
    set_charging_plan的逻辑还没有完成
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2025-01-23 添加电路接线图
    画了电器元件然后接了个线
    [Circuit Diagram.kicad_pcb, Circuit Diagram.kicad_sch]
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2025-01-23 更改文件目录结构，新增GPIO重构文件
    更改文件目录结构
    新增GPIO重构文件
    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
    [Circuit Diagram.kicad_pcb, Circuit Diagram.kicad_sch]
2025-01-24 更新代码
    补全了ModbusIO
    重命名了两个轮询线程
    补全了两个轮询线程
    更改了GPIO项目图
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2025-01-24 修复self.__class__的错误
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2025-01-27 修复初始化定义错误
2025-01-27 修复初始化错误
2025-01-27 修复bug
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2025-01-30 新增调试文字输出，补增变量注解，修复部分bug
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2025-02-02 修正shelly初始可用性为False
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2025-02-02 修复充电符合预期后无法停止的问题
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2025-02-03 上传图表文件
    [测试列表.ods]
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2025-03-15 更新3d打印基座模型
    [HV_Teil.FCStd, HV_Teil.stl, LV_Teil.FCStd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]
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2025-03-16 Update _Charge_Unit.py
    增加直接充电的逻辑
    增加手动传入数据逻辑(充电时不更新充电计划表)
    修改 get_current_limit 的赋值逻辑, 确保 self.__current_limit, self.__current_min, self.__current_max一直存在有效值(>=0)
    修改 charging 中的 charge_duration_sec 计算逻辑, 改为每次用下次开始时间减去当前实际时间, 以避免存在累计误差
2025-03-16 Update _Data_Collector.py
    增加停止方法, 用于对象销毁时可以更好管理线程，避免内存泄漏
    降低发送文字和图片的频率，如果内容为空，则不发送
    完善发送图片的逻辑
2025-03-16 Update _GPIO_Manager.py
    增加对象销毁的方法
    适配手动添加计划表的函数
2025-03-16 Update Manager_Coroutine.py
    增加对象销毁方法
    增加停止方法
2025-03-16 Update Port_OCPP_WebSocket_Client.py
    修复非OCPP消息接收时的信号传递时,数据类型不对的问题
2025-03-16 Update Port_WebSocket_Server.py
    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
2025-03-16 修改测试模拟软件
    增加对意外报错退出的错误跟踪
    修复因数据类型问题造成的软件崩溃问题
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2025-03-19 Update _Charge_Unit.py
    增加向网页发送信息的信号，
    修正停止充电后仍可以启动的bug
    [_Charge_Unit.py]
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2025-03-23 修复stop的bug
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2025-03-26 修复Shelly地址问题，修复直充不检查的问题
2025-03-27 修复 模拟器 数值比较错误
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2025-03-30 更新底座3d模型
    [HV_Teil.FCStd, HV_Teil.stl, LV.SLDPRT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]
2025-03-30 删除模型
    [LV.SLDPRT, Rohr.SLDPRT]
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2025-04-07 上传论文Latex文件
    [tudathesis.cfg]
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2025-04-15 修复充电条件判断错误 以及 增加shelly重置失败是的重试
2025-04-15 完善 reset 地址的逻辑
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2025-04-15 增加进程文件锁，修复ledbug
2025-04-16 更新EVSE测试，exe中显示有问题，未修改
    [Motor.json]
2025-04-16 修复 线程锁 bug
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2025-04-16 修复部分bug
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2025-04-18 解决停止时，计时器仍在进行其他操作，但此处仍存在问题，创建计时器前没有对是否充电程序在运行做判断
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2025-04-18 修复写入错误以及读取方式
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
